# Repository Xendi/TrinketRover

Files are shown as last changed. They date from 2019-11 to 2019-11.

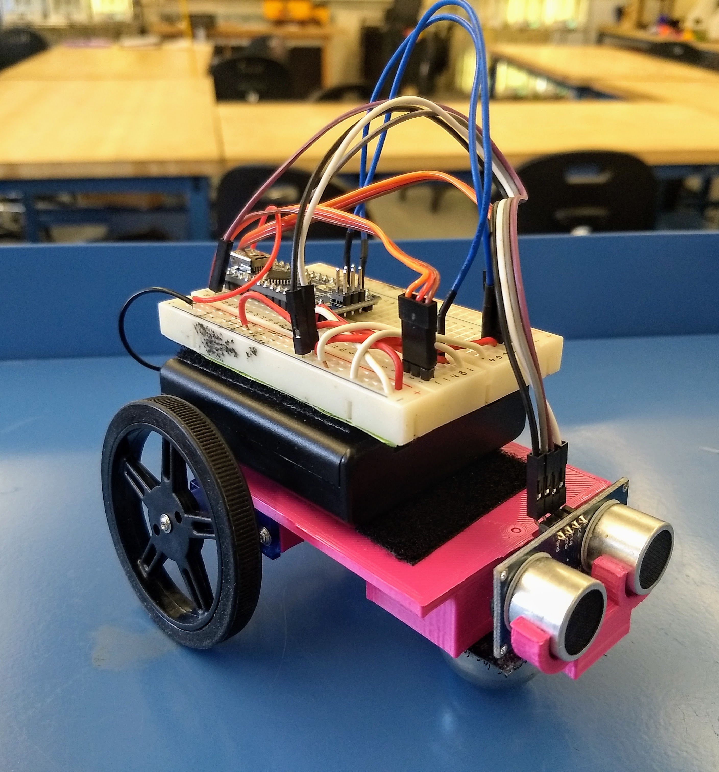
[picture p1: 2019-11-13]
NanoRover/pictures/nanoRoverV3.jpg

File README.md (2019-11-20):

Nano Rover (previously Trinket Rover)
============
STEM / STEAM curriculum is gaining momentum in k-12 education. It's exciting, but there are some significant obstacles to manage: not all teachers have the technical expertise (or time) to generate curriculum, cost of materials can be prohibitive, and sourcing good quality components can be time consuming.

The aim of this project is to provide a low-cost but high-quality open software / open hardware platform for teaching robotics to students of all ages.

Instructions
============

Build instructions for the original rover are at:
https://learn.adafruit.com/trinket-powered-rover/red-rover

The Bergen Makerspace version is beefed up a little by replacing the Trinket with an Arduino Nano, which is not much bigger and provides full Arduino functionality and digital pins, for only a couple of dollars more than the Trinket. 
We are using a different sonar module too, the HC-SR04, which has separate trigger and echo pins.

The wiring diagram is slightly different for the Nano version, see the /circuit folder.

Connections
===========

Sonar Trig Pin - 			Nano Pin D13
Sonar Echo Pin - 			Nano Pin D12
Right Servo Data Pin - 			Nano Pin D4
Left Servo Data Pin - 			Nano Pin D2
Power: 4xAA 1.5V  			Nano Vin/GND  

We sourced continuous rotation servo motors for almost the same price as regular ones, so you don't have to modify your own! They will still use the Adafruit Softservo library, so be sure to install it to your Arduino IDE hardware folder:
https://github.com/adafruit/Adafruit_SoftServo

You can 3D print your own chassis, using the STLs found here, or design your own! Rick made the originals in TinkerCAD, so bonus points for anyone who makes a parametric version in OpenSCAD!

The target price for all electronics / hardware is ~ $25. Plastic parts can be produced on-site for ~ $2 each if the school has a 3D printer.

#####3D Printing
------
 * Chassis (mustache now fully integrated)

#####Electronics
------
 * Arduino Nano
 * HCSR04 Ultrasonic Sensor
 * Continuous Rotation Micro Servos
 * Female / Male Jumpers

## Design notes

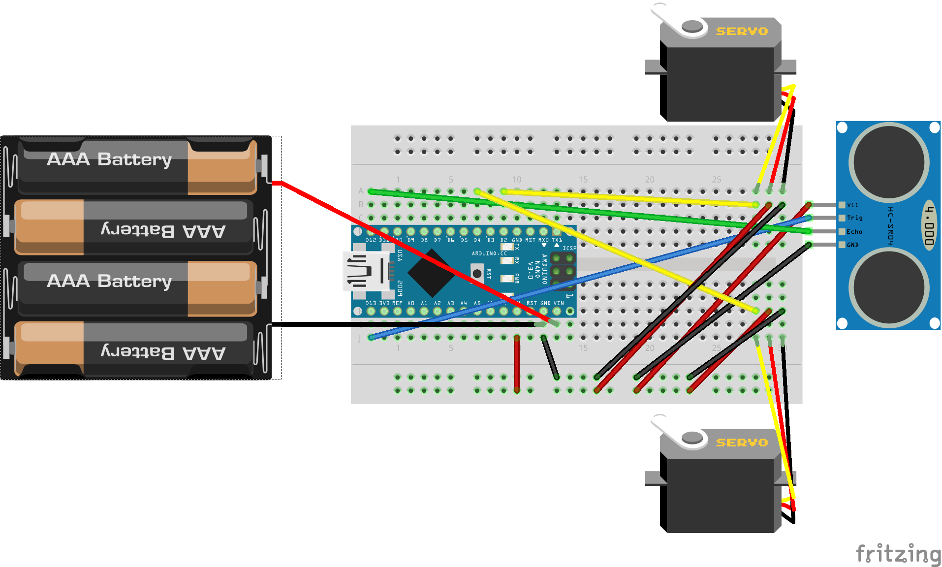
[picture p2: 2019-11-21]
NanoRover/circuit/nanorover.png

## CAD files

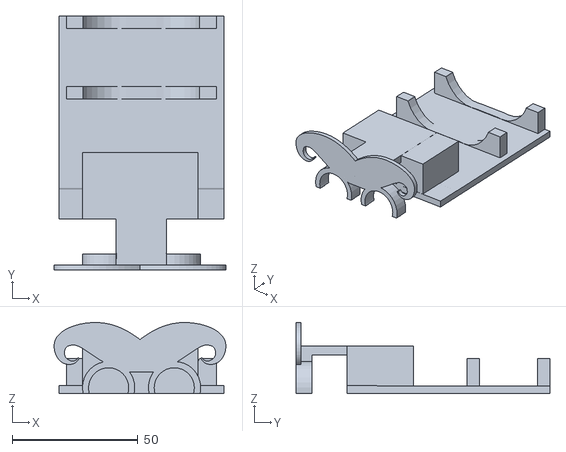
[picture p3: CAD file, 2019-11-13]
NanoRover/models/NanorobotV3.stl
68.3 x 101.0 x 28.2

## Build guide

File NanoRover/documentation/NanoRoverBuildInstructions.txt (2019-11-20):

NanoRover Build Instructions
****************************

1)  Use two small self-tapping screws to attach each servo to the left and right servo mounts on the plastic chassis. Mount the motors with the wires to the rear of the chassis. Push fit one wheel to each servo and secure with a single large-rim screw.

2) Place 4 AA batteries in the battery pack, and turn the switch to OFF

3) Use Velcro (1" strip) to attach the battery pack to the chassis. Position the battery pack with the switch down, sticking out over the rear end of the chassis so that it remains accessible. 

4) Use Velcro to attach the mini breadboard to the battery pack. 

5) Wire up the breadboard with all the components as in the circuit diagram or breadboard diagram. 

6) Slot the sonar module into the eye sockets at the front of the chassis.

7) Use Velcro to attach the nosewheel under the chassis at the front. 

8) If necessary, use Arduino IDE to upload nanorover.ino (you may need to install Adafruit's Softservo library if you haven't already). 

9) Turn the battery pack switch to ON. Robot!

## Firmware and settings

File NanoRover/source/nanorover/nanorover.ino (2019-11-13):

//*** original Trinket-powered Micro Rover by Rick Winscot, via Adafruit
//*** modified for Arduino Nano by David Reeves 2014, 2019
//*** Added 7 segment display readout and photoresistor-stall mechanism (neither required for operation)


#include <Adafruit_SoftServo.h>                  // install these two libraries in your IDE
#include <SoftwareSerial.h>
 
#define SERVO1PIN 2   // Servo control line (orange) on Nano Pin #2
#define SERVO2PIN 4   // Servo control line (orange) on Nano Pin #4
 
Adafruit_SoftServo servo_left, servo_rght;      
 

// Connect the sonar signal pins to these pins on the Nano.
#define trigPin 13
#define echoPin 12


#define segPin 8  // used to connect to 7 segment display serial Rx
const int analogInPin = A0;
int sensorValue = 0; 
SoftwareSerial mySerial(7, segPin);  // Tx from arduino is pin 8, connect to Rx on SFE LED Serial
  
 
// Moderate speed forward for both servos. Given the orientation of the servos
// one will be going forward, and the other backward. You may need to adjust 
// these slightly to get the rover to move straight forward.

const int left_offset = -8;             //  adjust this if necessary to make rover go straight
const int right_offset = 1;             //  adjust this if necessary to make rover go straight
int left_speed = (120+left_offset);
int right_speed = (60+right_offset);
 
// Number in cm when the rover will reverse and try to navigate around.
const int obstacle = 20;
 
// Multiplier used to determine how far the rover will back-up.
const int back_track = 100;
 
// Duration of a ping, distance in inches, distance converted to cm.
long duration, inches, cm;
int avoid_direction, turn_angle, turn_count;
 
void setup() 
{  
  Serial.begin (9600);
  randomSeed(analogRead(0));
  pinMode(trigPin, OUTPUT);
  pinMode(echoPin, INPUT);
  pinMode(segPin, OUTPUT);
 
  
 
  // Attach servos... and off we go!
  servo_left.attach(SERVO1PIN);
  servo_rght.attach(SERVO2PIN);
  
  mySerial.begin(9600);
  delay(50);
  mySerial.print(0x76); // reset the 7 segment display
  mySerial.print("hiya"); //Hello world!
  
  turn_count = 0;
} 
 
void loop() 
{ 
  // Setting servos in forward motion.
  servo_left.write(left_speed );
  servo_left.refresh();
  servo_rght.write(right_speed );
  servo_rght.refresh();
  delay(15);  
 

  
  // establish variables for duration of the ping, and the distance 
  // result in inches and centimeters.
  duration = 0;
  inches = 0;
  cm = 0;
 
  // The PING))) is triggered by a HIGH pulse of 2 or more microseconds.
  // Give a short LOW pulse beforehand to ensure a clean HIGH pulse:

  digitalWrite(trigPin, LOW);  // Added this line
  delayMicroseconds(2); // Added this line
  digitalWrite(trigPin, HIGH);
  delayMicroseconds(10); // Added this line
  digitalWrite(trigPin, LOW);

 
  // The echo pin is used to read the signal from the PING))): a HIGH
  // pulse whose duration is the time (in microseconds) from the sending
  // of the ping to the reception of its echo off of an object.

  duration = pulseIn(echoPin, HIGH, 10000);
  
  if (duration == 0) {
    duration = 10000;    // a 0 return means no echo was heard - default to a high value instead to avoid errors
  }
  
  // convert the time into a distance.
  inches = microsecondsToInches(duration);
  cm = microsecondsToCentimeters(duration);  
 
  if (cm < 1000) {    // right-align the 7seg display
    mySerial.print(" ");
  }
    
  if (cm < 100) {
    mySerial.print(" ");
  }
      
  if (cm < 10) {
   mySerial.print(" ");
  }

  String c = String(cm);
  mySerial.print(c);    // print distance in cm on 7seg display
 
 // obstacle avoidance - 50-50 chance of backing up left or right
 
  if ( cm < obstacle ) {
    // back_track * delay(15) = distance the rover will back-up during 
    // obstacle avoidance.
    
    //turn_count+=1;
    //String t = String(turn_count);
                
                
    avoid_direction=random(0,2);             //  Set up object avoidance method
       // 50% chance of backing up left or right   
    if (avoid_direction == 0) {
      turn_angle = 60;
    }
    else {
      turn_angle = -60;
    }
      
    
    for (int i = 0; i < back_track; i++) {
      
      servo_left.write(90+left_offset+turn_angle);
      servo_left.refresh();
      servo_rght.write(90+right_offset+turn_angle);
      servo_rght.refresh();  
      delay(15);
    }
  }
  
  if (cm >= 200 || cm <= 0){
    Serial.println("Out of range");
  }
  else {
    Serial.print(cm);
    Serial.println(" cm");
  }

 
  // read photoresistor on pin A0, vs 4.7kohm resistor
  // if photoresistor is high-resistance or absent, run motors, otherwise stop 
  //  sensorValue = analogRead(analogInPin);      
  
  while (sensorValue > 400) {
    sensorValue = analogRead(analogInPin); 
    servo_left.write(90);
    servo_left.refresh();
    servo_rght.write(90);
    servo_rght.refresh();  
    delay(150);
  }
 

}


// Functions below

 
long microsecondsToInches(long microseconds)
{
  // According to Parallax's datasheet for the PING))), there are
  // 73.746 microseconds per inch (i.e. sound travels at 1130 feet per
  // second).  This gives the distance travelled by the ping, outbound
  // and return, so we divide by 2 to get the distance of the obstacle.
  // See: http://www.parallax.com/dl/docs/prod/acc/28015-PING-v1.3.pdf
  return microseconds / 74 / 2;
}
 
long microsecondsToCentimeters(long microseconds)
{
  // The speed of sound is 340 m/s or 29 microseconds per centimeter.
  // The ping travels out and back, so to find the distance of the
  // object we take half of the distance travelled.
  return microseconds / 29 / 2;
}

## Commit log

2014-05-29 breadboard layout for nano
    [nanorover.fzz]
2019-11-13 V3 files added and reorganised
    [NanorobotV3.stl, nanorover.fzz]
2019-11-13 tidied up code
    [nanorover.fzz]
2019-11-13 Reorganised nanorover files
    [chassis_large.stl, chassis_small.stl, customizable rover.scad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]
2019-11-21 updated breadboard diagram
    [nanorover.fzz]
